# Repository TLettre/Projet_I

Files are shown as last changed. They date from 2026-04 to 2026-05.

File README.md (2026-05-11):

# Projet intégrateur 2: dashboard de trottinette
Projet Final de Projet Intégrateur 2.

## Mise en contexte

Le projet consiste à développer, programmer et assembler
un tableau de bord qui est fixé sur une trottinette électrique
complètement fonctionnelle à l’aide d’un boitier. Ce système 
électronique complet est supposé établir une communication avec le module
de contrôle, récupérer les données essentielles, traiter puis
présenter ces données ainsi que permettre au conducteur de visualiser
l’état du véhicule en temps réel.  

Dans ce fichier, il sera possible de voir la totalité des éléments présents autant en 
documentation que fonctionement au niveau du tableau de bord de la trottinette.

## Prérequis

### Matériel:
- Le PCB doit être alimenté avec 12V et 50mA.
- Le module de contrôle utilisé doit être le STM32U083CC.
- Le STM32U083CC doit être alimenté par un cable USB-C.
- Le dashboard doit être affiché sur un écran avec un cable USB-C à HDMI.
- Le PCB doit contenir un bouton de réinitialisation.
- Le branchement du connecteur JST qui est branché à la trottinette est définit dans le document de branchements.
- Nous avons ajouté des DELs d'alimentation pour chaque niveau d'alimentation, bien que ce requis était optionnel.
- Il doit y avoir 5mA maximum pour chaque DEL.
- Le PCB doit être fixé avec 4 vis M3.
- Nous avons fait la conception d’un boitier ergonomique pour encapsuler l’électronique, bien que ce requis soit optionnel.
- Le boitier doit pouvoir être bien fixé sur le guidon de la trottinette.
- Les dimmensions du PCB doivent être de 5cm par 5cm.
- Le PCB ne doit pas être accessible à l'usager.
- Les DELs d'alimentation ne doivent pas être accessibles à l'usager.
- Le boitier doit être simple à imprimer.

### Logiciel:
- Le module de contrôle et le tableau de bord doivent communiquer par protocole UART.
- Les données sont transmises par le module de contrôle dans un format JSON.
- Les informations suivantes doivent être affichées : la commande envoyée au moteur, la vitesse du véhicule, le pourcentage de charge de la batterie, le courant consommé, la température du système, l'état de l’éclairage, et l'information de freinage.
- L'affichage doit être ergonomique.
- L'information affichée doit être en temps réel.
- Le délai de rafraichissement doit être 4 fois par secondes.
- L'information affichée sur l'écran doit être épuré, clair, visible et compréhensible.

### Limitations:
- Nous ne connaissions pas l'ampleur du projet, ce qui a beaucoup affecté l'organisation de notre projet.

## Documentation

Voici les différents documents qui se retrouvent dans le Github ainsi que la fonction de chacun.

[**Boitier**:](https://github.com/TLettre/Projet_I/blob/a2e4f342a44780944c0242c8f5481d343143d4d6/Boitier.zip)
Le fichier Boitier.zip contient les documents de la modélisation du boitier 3D. Tous les fichiers qui étaient nécessaires à l'impression se trouvent dans ce fichier.

[**Cahier des charges**:](https://github.com/TLettre/Projet_I/blob/81377b3d7a6bdb845bd9907a101511ad725f1cf8/Cahier_charges.docx)
Ce fichier contient toutes les informations concernant le projet. 
- Mise en situation et schéma de concept (p.3)
- Requis techniques et inconnus u projet (p.4-5)
- Livrables et échéancier (p.5-6)
Ce fichier regroupe donc toutes les informations que nous avions concernant le projet.

[**Schéma bloc**:](https://github.com/TLettre/Projet_I/blob/feae1b3e02cbf4ebef9064a34becacfc2022ecb2/Notes/ProjetIntegrateur2.drawio)
Schéma qui explique le fonctionnement de notre PCB.

[**Schéma électrique**:](https://github.com/TLettre/Projet_I/blob/main/Altium/PI2_Circuit.SchDoc)
Ce fichier contien le schéma électrique du tableau de bord. 
- Le régulateur et la bobine ne sont pas les bonnes pièces.

[**PCB**:](https://github.com/TLettre/Projet_I/blob/main/Altium/PI2_PCB_2L.PcbDoc)
Fichier Altium du PCB complet du tableau de bord.
-  Les footprints de la bobine, du régulateur et des boutons ne sont pas les bonnes.

[**BOM**:](https://github.com/TLettre/Projet_I/blob/96cb56f76c8dbb2d10cd777ee212bbd68585368f/Altium/BOM.pdf)
Ce fichier contient les informations importantes de chacunes des pièces soudées sur le PCB.
-  La bobine et le régulateur ne sont pas les bonnes pièces et on été remplacées sur le PCB.

[**Code STM32**:](https://github.com/TLettre/Projet_I/blob/main/Code/code%20du%20stm32.c)
Code pour le fonctionnement du PCB.
- Il devrait prendre les données du fichier JSON et les envoyer vers le Raspberry Pi par UART.
- Des explications plus précises concernant le code se trouvent dans les commentaires du code.

[**Code Raspberry Pi**:](https://github.com/TLettre/Projet_I/blob/main/Code/code_pi.py)
Code qui permet de récupérer les donnés en JSON et de les envoyer sur l'écran.
- Des explications plus précises concernant le code se trouvent dans les commentaires du code.

Tout autre fichier de programmation sert à exécuter des tests.

## Guide d'utilisation

**Démarage**: Le tableau de bord devrait démarrer lorsque la trottinette est mise en marche.
		
### Mode de fonctionnement pour un utilisateur:
Les données ci-dessous devraient être visibles sur l'écran dès que la trottinette est activée:
- Vitesse de la trottinette (en km/h)
- Pourcentage de la batterie
- Courrant consommé (en ampères)
- Température du système (en degrés celsius)
- État de l'éclairage (on ou off)
- Information de freinage (on ou off)

Lorsque la trottinette est en mode freinage, il est impossible d'accélérer.
		
[**Image du Dashboard en action**](https://github.com/TLettre/Projet_I/blob/6009a4685d689ea0507f30d0aa41ed84b18c9245/Code/dashboard%20trotinette.png)

### Pour un développeur:
- La DEL D1 verte indique le fonctionnement du 12V.
- La DEL D2 rouge indique le fonctionnement 3.3V.
- Le bouton S1 permet de faire un RESET du PCB.
- Le bouton S2 permet de BOOTer le PCB pour envoyer un nouveau code dans le microcontrôleur.

## À terminer
- Le BOOT ne fonctionne pas, donc il faudrait l'arranger.
- La communication entre le PCB et le Raspberry Pi en UART ne fonctionne pas.

**Auteurs**: Amélie, Tristan et Gauthier

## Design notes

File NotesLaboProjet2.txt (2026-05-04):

Semaine 1
Tristan: 
	- recherche dans les fiches techniques et schéma électrique
	- recherche sur le régulateur switching et son branchement
	- branchement du régulateur switching
	- rechercher les pièces importantes et trouver leurs symboles dans Altium
	- faire les symboles et les traces des pièces s'ils n'existent pas
Amélie: 
	- recherche dans les fiches techniques et schéma électrique
	- recherche sur le régulateur switching et son branchement
	- branchement du régulateur switching
	- recherche sur le connecteur et son branchement
	- branchement du connecteur
Gauthier: 
	- recherche dans les fiches techniques et schéma électrique
	- recherche sur le régulateur switching et son branchement
	- branchement du régulateur switching
	- recherche sur le MCU et son branchement
	- commencer le branchement du MCU

- Nous avons créé les symboles et les traces des pièces dont nous ne les avions pas.
- Nous avons trouvé toutes les pièces importantes (écran, connecteurs, BMI323) dont nous avions besoin dans le schéma.
- Nous avons fait beaucoup de recherches sur le branchement du régulateur switching et nous avons fait le branchement.
- Nous avons débuté la recherche et le branchement du MCU
- Manque temps schéma électrique: sous estimé le temps et la recherche nécessaire, beaucoup temps recherche LDO

--------------------------------------------------------------------------------------------------------------------------------------------------------------------------------------------

Semaine 2
Tristan: 
	- continuer la recherche dans les fiches techniques et schéma électrique
	- finir recherche du MCU et son branchement
	- finir le branchement du MCU
	- recherche et branchement du BMI323
	- envoyer le BOM
Amélie: 
	- continuer la recherche dans les fiches techniques et schéma électrique
	- finir recherche du MCU et son branchement
	- finir le branchement du MCU
	- recherche et branchement du BMI323
	- envoyer le BOM
Gauthier: 
	- continuer la recherche dans les fiches techniques et schéma électrique
	- recherche et branchement de l'écran
	- recherche et branchement du BMI323
	- envoyer le BOM

- Nous avons fait la recherche et le branchement de l'écran
- Nous avons fait la recherche et le branchement du BMI323
- Nous avons terminé la recherche et le branchement du MCU
- Rencontre pour les reviews: nous avons décidé d'envoyer le BOM avant d'avoir eu la vérification du schéma
- Le client a changé certaines pièces à utiliser puisqu'il y avait une erreur. Il a donc fallu faire la recherche de ces pièces et les symboles si nécessaire.

--------------------------------------------------------------------------------------------------------------------------------------------------------------------------------------------

Semaine 3
Tristan: 
	- finir le schéma
	- brancher les DELs d'alimentation
	- finir le branchement de chaque pièce
	- brancher les pièces entre elles
	- séparer le schéma dans des parties clairement identifiées pour organiser le schéma
	- s'assurer d'avoir ajouté les notes nécessaires pour comprendre de le schéma
Amélie: 
	- finir le schéma
	- finir le branchement de chaque pièce
	- brancher les pièces entre elles
	- séparer le schéma dans des parties clairement identifiées pour organiser le schéma
	- s'assurer d'avoir ajouté les notes nécessaires pour comprendre de le schéma
Gauthier: 
	- finir le schéma
	- finir le branchement de chaque pièce
	- brancher les pièces entre elles
	- séparer le schéma dans des parties clairement identifiées pour organiser le schéma
	- s'assurer d'avoir ajouté les notes nécessaires pour comprendre de le schéma

- Nous avons fait la recherche et le branchement de chacun des connecteur
- Nous avons fait le branchement des DELs d'alimentation
- Nous avons organisé le schéma et identifié chaque partie du schéma

--------------------------------------------------------------------------------------------------------------------------------------------------------------------------------------------

Semaine 4
Tristan: 
	- corriger les erreurs du schéma
	- corriger certaines erreurs dans le schéma
	- faire le routage du PCB
	- finir le routage du PCB en dehors du cours
	- régler les problèmes du schéma et du PCB
Amélie: 
	- corriger les erreurs du schéma
	- faire le boitier
	- finir la modélisation du boitier en dehors du cours
	- aider Tristan à finir le schéma
	- il faut attendre que le schéma soit fini afin de commencer la modélisation pour avoir les mesures du PCB, ce qui a retardé la modélisation du boitier
	- régler les problèmes du schéma et du PCB
Gauthier: 
	- commencer le code
	- faire la recherche nécessaire (sur le Raspberry Pi) afin de pouvoir faire le code
	- préparer le corps du code (les parties nécessaires et comment le code sera construit)
	- faire la recherche nécessaire pour commencer à coder les parties essentielles
	- régler les problèmes du schéma et du PCB

- Nous avons du annuler plusieurs reviews puisque le schéma nous a demandé beaucoup plus de temps que ce que nous avions prévu.
- L'écran a été remplacé par un Raspberry Pi. Nous avons dû faire la recherche pour le Raspberry Pi puisque ce remplacement était un imprévu.
- Lors de cette semaine, nous avons du faire beaucoup de travail en dehors du cours pour finir les livrables à temps.
- Nous avons commencé à faire beaucoup plus de documentation concernant notre travail et l'utilisation de notre projet.

--------------------------------------------------------------------------------------------------------------------------------------------------------------------------------------------

Semaine 5
Tristan: 
	- créer un GitHub pour y mettre tous ce qui a été fait pour le projet jusqu'à maintenant
	- commencer le guide d'utilisateur
		=> explication des modes dans le guide d'utilisateur
		=> explication du démarrage
		=> explication de ce qui est afficher
Amélie:
	- terminer le boitier
	- vérifier que les mesures du boitier fonctionnent avec le PCB
	- faire imprimer le boitier
	- commencer le plan de tests
		=> prendre le gabarit utilisé dans le cours de Circuit Imprimé 2
		=> remplir l'entête du document
		=> commencer à inscrire les tests qui devront être fait
Gauthier:
	- faire les recherches nécessaires pour la programmation
	- commencer la programmation
		=> créer des espaces/fenêtres pour chaque chose qui devra être affichée

- Nous avons décidé de commencer le guide d'utilisateur plus tôt afin de recevoir le plus de commentaires possibles lors de la rétroaction formative.
- L'écran ne doit plus être utilisé dans le projet, donc nous avons moins de recherches à faire cette semaine ce qui nous permet de prendre de l'avance.
- Nous avons créé un GitHub pour y mettre tous ce que nous avons fait dans le projet jusqu'à maintenant.

--------------------------------------------------------------------------------------------------------------------------------------------------------------------------------------------

Semaine 6
Tristan:
	- terminer de mettre tous les fichiers dans le Github
	- continuer le guide d'utilisateur
	- continuer le plan de tests
	- aider Gauthier avec le code
Amélie:
	- correction des mesures du boitier
	- réimprimer le boitier corrigé
	- finir le plan de test
Gauthier:
	- continuer la programmation
		=> finir la fenêtre d'interface
		=> afficher les informations reçues par le microcontrôleur
		=> recherche et amélioration du code de l'interface graphique 
		=> revoir certains bloc comme la vitesse
		=> améliorer le mode erreur

- Nous avons fait une analyse de rétroaction formative avec l'enseignant.
- Nous n'avons pas reçu le PCB que nous avons fait. Nous avions prévu de le recevoir cette semaine et de faire la soudure. Cette partie de la planification doit donc être reportée.

--------------------------------------------------------------------------------------------------------------------------------------------------------------------------------------------

Semaine 7
Tristan:
	- Tristan était absent et n'a pas eu l'occasion d'avancer le projet pendant la semaine
Amélie:
	- finir le plan de test
	- continuer le guide d'utilisateur
Gauthier:
	- continuer la programmation
		=> début du code pour la transmission en UART
		=> traduction du JSON dans le code STM32 puis renvoie les données brutes dans le rasberry

- Tristan était absent pendant cette période. Il n'a donc pas pu faire la soudure pendant le cours. Il va falloir travailler d'avantage pendant la semaine pour rattraper notre retard et redistribuer les tâches pour ce cours si nécessaire.
- Tristan est absent et n'a pas mis le guide d'utilisateur (commencé et presque terminé) sur le GitHub. Il est le seul à y avoir accès. Il va devoir le mettre dans le Github dès que possible et l'envoyer à l'enseignant rapidement pour avoir la rétroaction formative du guide d'utilisateur.
	=> Tristan a envoyé le guide d'utilisateur. Le guide d'utilisateur a été ajouté au GitHub et envoyé à l'enseignant pour la rétroaction formative.

--------------------------------------------------------------------------------------------------------------------------------------------------------------------------------------------

Semaine 8
Tristan: 
	- déterminer les pièces qui devront être soudées sur le PCB
	- prendre les pièces disponibles en classe
	- demander les pièces au magasin
	- faire la soudure lorsque les pièces seront reçues
	- faire la documentation de la partie électronique du projet dans le guide d'utilisateur
Amélie:
	- continuer le guide d'utilisateur
	- déterminer les tests nécessaires pour le boitier dans le plan de tests
	- faire la documentation de la partie mécanique du projet dans le guide d'utilisateur
Gauthier: 
	- terminer la programmation
		=> abandonner l'idée de traduire le code STM et juste créer un canal ouvert pour le STM il transfert juste les données sans décodera
		=> avancement sur le code du stm32
	- déterminer les tests nécessaires pour la programmation dans le plan de tests
	- faire la documentation de la partie programmation du projet dans le guide d'utilisateur
	
- Puisque nous n'avions pas les pièces pour souder le PCB, nous n'avons pas eu l'occasion de faire la soudure lors de la semaine précédente. Tristan devra donc faire la soudure pendant la semaine lorsque les pièces seront reçues.
- Nous avons eu de la difficulté à obtenir une version à jour du BOM. Nous avons fait quelques changements au schéma électrique entre la remise du BOM et la remise du PCB. Nous n'avons ajouté que quelques petites pièces faciles à avoir (résistances). 
- Lorsque nous avons reçu nos pièce, il y avait une inductance que le magasin n'avait pas. Il n'y avait aucun équivalent de cette pièce. Nous avons donc du chercher une autre inductance qui pourrait fonctionner dans notre circuit.
- Les traces prévues pour l'inductance sont en surface mount, alors que l'inductance est pour du through hole, ce qui rend la soudure plus difficile. Heureusement, la place dédiée à l'inductance était proche du bord du PCB. Nous l'avons donc soudue de côté.
- L'inductance de remplacement est beaucoup plus grosse que la précédente. Nous avons donc dû faire un trou dans notre boitier pour que le PCB soudé puisse entrer dans le boitier.
- Les boutons étaient trop petits pour les traces dédiées. Nous avons donc dû faire des ponds de soudure entre les boutons et les pads.

--------------------------------------------------------------------------------------------------------------------------------------------------------------------------------------------

Semaine 9
Tristan:
	- terminer la soudure du PCB
	- remplir le plan de test du PCB
	- faire l'intégration
	- aider Gauthier avec les tests pour le code
Amélie:
	- terminer le guide d'utilisateur
	- préparer la présentation
	- faire et compléter le plan de tests pour le boitier
	- faire l'intégration
Gauthier:
	- tester la programmation avec le Raspberry Pi
	- faire la documentation de la partie programmation du projet dans le guide d'utilisateur
	- remplir le plan de test de la programmation
	- faire l'intégration

- La remise formative du guide d'utilisateur n'a pas été faite. Il y a eu une mauvaise communication dans l'équipe. Nous avons donc remis le guide d'utilisateur en retard et nous avons eu les commentaires de l'enseignant en retard.
- Nous n'avions pas regardé les commentaires de l'enseignant sur les choix des pièces dans le BOM. Le régulateur que nous devions mettre ne fonctionne donc pas. Nous avons donc du souder des fils et alimenter la sortie du régulateur avec du 3.3V pour être en mesure d'exécuter les tests.
- Le prototype n'est toujours pas fonctionnel. Le PCB supporte les tensions et les del de statut fonctionnent. L'ordinateur semble capter le Raspberry Pi et le code semble être envoyé. Donc, la programmation ne fonctionne probablement pas. Sinon, il pourrait y avoir un problème pour la connection entre le PCB et le Raspberry Pi.
- Il y a eu des problèmes avec la programmation. Le code a été testé avant qu'il soit terminé. Certaines fonctions étaient définies, mais pas appelées. Les librairies qui étaient nécessaires au code n'étaient pas envoyées dans le GitHub. Le code manque énormément de commentaire, ce qui rend le code difficile à comprendre pour les autres coéquipiers. Il y a certains aspects du code qui n'ont pas été appris en classe, ce qui rend le code peu commenté encore plus difficile à comprendre pour les autres coéquipiers.
- Le boitier n'était pas assez grand pour un des condensateur. Il a donc fallu faire un autre trou dans le couvercle du boitier pour que le boitier puisse se fermer.

--------------------------------------------------------------------------------------------------------------------------------------------------------------------------------------------

Semaine 10
Tristan:
	- faire fonctionner le prototype du projet
	- terminer de remplir le plan de tests
	- terminer le guide d'utilisateur
	- présenter notre projet
Amélie:
	- faire fonctionner le prototype du projet
	- terminer de remplir le plan de tests
	- terminer le guide d'utilisateur
	- présenter notre projet
Gauthier:
	- faire fonctionner le prototype du projet
	- terminer de remplir le plan de tests
	- terminer le guide d'utilisateur
	- présenter notre projet

- Nous avons réalisé que le BOOT de notre PCB ne fonctionne pas. Afin de régler ce problème, il faudrait refaire le PCB, puisque nous pensons que le problème est dans notre branchement. Nous n'avons pas le temps de régler ce problème, donc notre prototype ne fonctionne pas.
- Nous sommes incapable d'envoyer notre code dans notre PCB. Nous pensons que c'est en raison du  mauvais fonctionnement de notre circuit de BOOT.

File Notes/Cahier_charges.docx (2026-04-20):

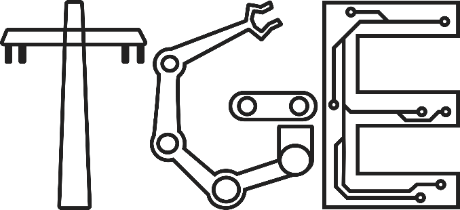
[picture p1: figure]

Technologie du génie électrique : Électronique programmable (243.G0)

TITRE
Amélie Sarrazin
Tristan Lettre
Gauthier Milossi

243-494-SH - Projet intégrateur 2
Présenté à : Prénom Nom

Date :

Table des matières

# 1. Mise en situation

## A. Acteurs du projet

- Équipe professorale de TGÉ du Cégep de Sherbrooke
- M. Gauthier (représentant d’ÉcoMobilité Sherbrooke)
- Les étudiants (public cible)
- Notre équipe

## B. Résumer du mandat

Le mandat consiste à développer, programmer et assembler un tableau de bord qui sera fixée sur une trottinette électrique complètement fonctionnelle, à l’aide d’un boitier. Ce système électronique complet devra établir une communication avec le module de contrôle, récupérer les données essentielles, traiter puis présenter ces données ainsi que permettre au conducteur visualiser l’état du véhicule en temps réel.

## C. Schéma de concept

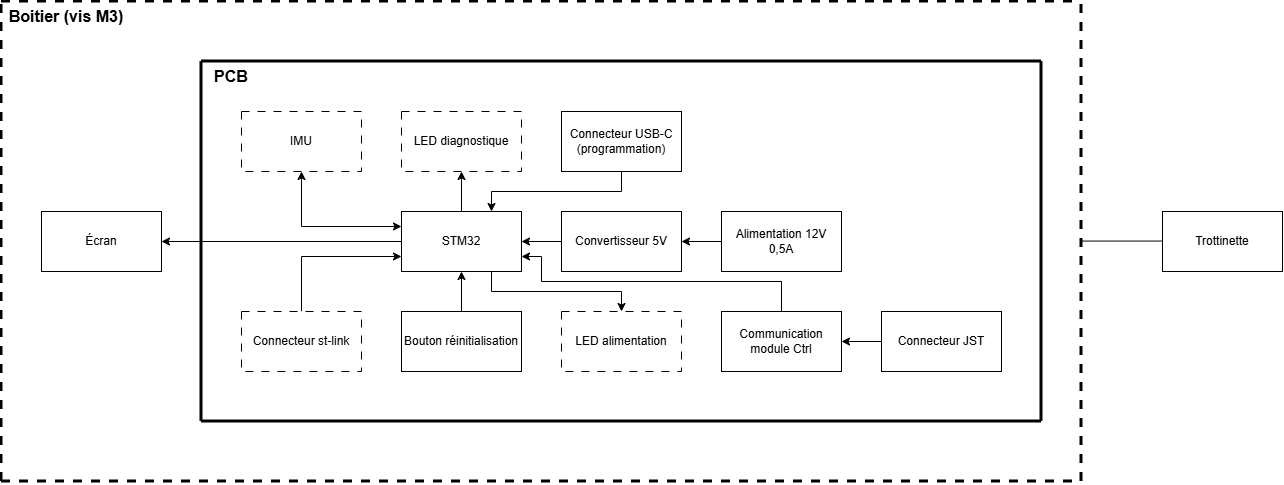
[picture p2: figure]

# 2. Requis technique

## A. Électrique

I. Essentiel | II. Optionnel
- Alimentation 12V 5mA - Module de contrôle (STM32U083MC) - STM32 (connecteur USB-C) - Écran (SMRVT50HQSFWN00) - Bouton de réinitialisation - Connecteur JST (branchement dans schéma) - Protocole UART entre le module de contrôle et le tableau de bord | - DEL d’alimentation pour chaque niveau d’alimentation - 2 DELs pull-up sur les broches GPIO 18 et 21 - 2 DELs pull-down sur d’autres broches GPIO - 5mA maximum pour chaque DEL - Connecteur ST-link - Accéléromètre (BMI323) - 2 boutons débogage

## D. Informatique

III. Essentiel | IV. Optionnel
- Protocole UART entre le module de contrôle et le tableau de bord - Données transmises par le module de contrôle dans un format JSON (spécifications envoyées par mio) - Informations affichées : Commande envoyée au moteur, vitesse du véhicule, pourcentage de charge de la batterie, courant consommé, température du système, état de l’éclairage, information de freinage (grisement de commande à l’écran) - Affichage ergonomique - Informations en temps réel - Délai de rafraichissement : 4 fois par secondes - Information sur l’écran : épuré, clair, visible et compréhesible | - 3 modes : initialisation, conduite et erreur - Mode conduite : affichages donnés facilement lisibles - Modes initialisation/erreur : affichage informations diagnostique spécifiques (codes erreur, état bouton arrêt urgence et état activation système) - Développement de code pour l’IMU - Logiciel de débogage

## E. Mécanique

V. Essentiel | VI. Optionnel
- Fixer le PCB avec 4 vis M3 - Fixé sur le guidon de la trottinette - Si l’IMU est présent, IMU centré et horizontal sur la carte - Essayer de garder le PCB 5 cm x 5 cm - PCB pas accessible à l’usager - Diodes d’alimentations pas visibles pour l’utilisateur - Écran bien visible à l’utilisateur - Boitier simple à imprimer - Boitier bien fixé au guidon | - Conception d’un boitier ergonomique pour encapsuler l’électronique

## F. Inconnus/risques

- Pinout du JST à 8 broches (branchement déjà défini, mais inconnu)
- Vitesse de transfert des données/affichage (temps réel)
- Est-ce qu’il faut que le projet soit résistant à l’eau?
- Requis de la résistance au climat
- Matériel du boitier
- Comment connecter fils au contrôleur?
- Communication entre carte et écran
- Taille de la trottinette/volant
- Structure/format du JSON
- Spécifications ergonomiques
- Ampleur du projet

## G. Livrables

- Prototype fonctionnel (circuit imprimé, assemblé, programmé et idéalement dans un boitier)
- Plan de test du prototype
- Guide utilisateur (explique comment utiliser interface)
- Documentation de fabrication complète (schéma électrique, dimensions, matériaux, fichier altium/fabrication et code)
- Présentation et démonstration

# 3. Échéancier

Bloc de travail (4h/semaine) | Tâches | | | Livrable
| Équipier 1 : Amélie | Équipier 2 : Tristan | Équipier 3 : Gauthier
1 | Lecture datasheets + schéma électrique | Lecture datasheets + schéma électrique | Lecture datasheets + schéma électrique | Dépôt cahier des charges
2 | Review schéma + BOM | Review schéma + BOM | Review schéma + BOM | Remise BOM
3 | Modélisation 3D | Routage | Configuration IOE et Github + programmation trottinette → PCB → écran
4 | Review modélisation 3D + routage + prog + fab PCB | Review modélisation 3D + routage + prog + fab PCB | Review modélisation 3D + routage + prog + fab PCB | Fab PCB + impression 3D
5 | Imprimer boitier + recherches/choisir protocole écran | Recherche + programmation StLink | Programmation trottinette → PCB → écran + mockup graphic + programmer graphic
6 | Assemblage boitier + plan de tests boitier | Soudage PCB + plan de tests PCB | Finir programmation | Analyse rétro formatif
7 | Intégration + plan de tests | Intégration + plan de tests | Intégration + plan de tests | Évaluation formative guide utilisateur
8 | Guide utilisateur + préparation présentation | Guide utilisateur + préparation présentation | Guide utilisateur + préparation présentation | Prototype fonctionnel
9 | Période buffer | Période buffer | Période buffer | Guide utilisateur
10 | | | | Présentation
11 | | | | Analyse rétro + guide utilisateur

Titre du projet

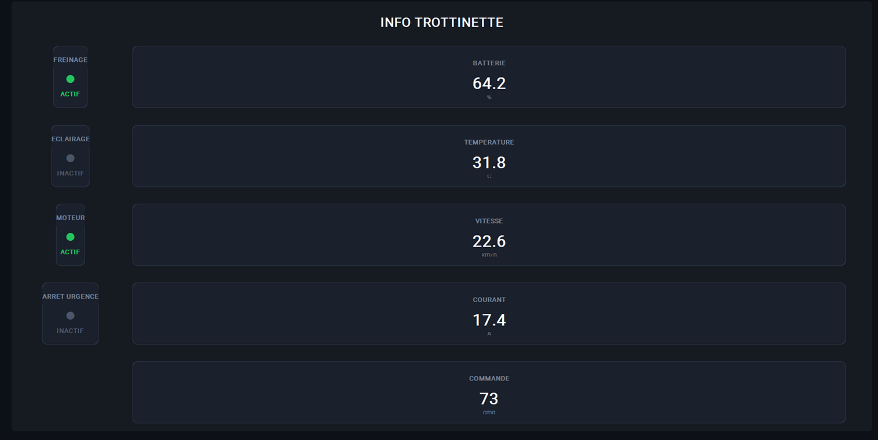
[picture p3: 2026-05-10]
Code/dashboard trotinette.png

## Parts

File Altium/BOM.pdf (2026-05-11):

Board | 1
Cours | 00

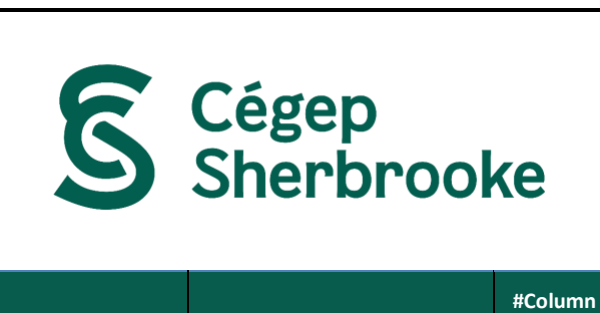
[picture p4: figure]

Item # | Designator | Layer | Description | Comment | Package / Case | Supplier 1 | Supplier Part Number 1 | Quantity | Quantity Total | #Column Name Error:' Note
1 | C1 | Top | WCAP-ASLI Aluminum Electrolytic Capacitors | 865080442004 | | | | 1 | #REF!
2 | C2 | Top | CAP ALUM 220UF 20% 25V SMD | EEE-1EA221UP | | | | 1 | #REF!
3 | C3 | Top | CAP CER 1UF 10V | 1µF | 0805 (2012 Metric) | DigiKey | 478-10611-1-ND | 1 | #REF!
4 | C4, C5 | Top | CAP CER 0.1UF | 0.1 µF | 0603 (1608 Metric) | DigiKey | 399- | 2 | #REF!
5 | D1 | Top | WURTH | 150080GS75000 | | | | 1 | #REF!
6 | D2 | Top | LED Uni-Color Red | 150080RS75000 | | | | 1 | #REF!
7 | J1 | Top | CONN HEADER | S10B-PHDSS (LF)(SN) | | | | 1 | #REF!
8 | J2 | Top | CONN RCP USB2.0 | DX07S016JA1R1500 | | | | 1 | #REF!
9 | J3 | Top | Connector Header | TSW-102-23-T-S | | | | 1 | #REF!
10 | L1 | Top | INDUCTOR, | B82432C1334K000 | | | | 1 | #REF!
11 | R1 | Top | RES 2K OHM 1% | 2 kOhms | 0603 (1608 Metric) | DigiKey | RMCF0603FT2K00CT-ND | 1 | #REF!
12 | R2 | Top | RES 270 OHM 1% | 270 Ohms | 0603 (1608 Metric) | DigiKey | 2019-RK73H1JTTD2700FCT-1 | | #REF!
13 | R3, R4 | Top | RES SMD 5.1K | 5.1 kOhms | 0603 (1608 Metric) | DigiKey | YAG3621CT-ND | 2 | #REF!
14 | R5 | Top | RES SMD 100K | | | | | 1 | #REF!
15 | S1, S2 | Top | SWITCH TACTILE | FSM4JSMA | | DigiKey | 450-1129-ND | 2 | #REF!
16 | U1 | Top | LM2574N-ADJG | LM2574N-ADJG | | | | 1 | #REF!
17 | U2 | Top | MCU 32-bit ARM | STM32U083CCT6 | | | | 1 | #REF!
18 | U3 | Top | Description | BMI323 | | | | 1 | #REF!

# Bill of Material

PI_2 | Concepteur Principal amélie
PI2 (243-494-SH) | Date du projet 09/02/26
Département Technologies du génie électrique | Date de génération du BOM 2026-04-20
Révision #NAME? | Heure de génération du BOM 10:01
Nombre de PCB 1 | Variant None

Commentaires ou instruction spécialies

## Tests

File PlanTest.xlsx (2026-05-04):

 |  | Plan de tests
 | Nom du PCB | PI_2 | Préparé par | Amélie Sarrazin
 | Cours | Projet Intégrateur 2 | Testeur | Tristan Lettre et Amélie Sarrazin
 | Département | Technologies du génie électrique | date | 2026-03-30
 | Révision du PCB
 | Fonction | Description du test | Résultat | Raison réussite ou échec | modification effectuée | Nouveau résultat | Commentaire
Électrique | Unitaire | Faire une inspection visuelle du PCB. | Réussi | Le PCB n'est pas endommagé, sauf pour des vias qui ne sont pas couverts et des pads un peu abimés. Les soudures sont correctes. Il n'y a aucun court-circuit. Il semble encore y avoir du flux qui pourrait causer des court-circuits, mais des tests de continuité ont été exécutés pour vérifier qu'il n'y a aucun court-circuit.
 | Unitaire | Vérifier qu'il n'y a aucun court-circuit entre le 12V et le GND, en mesurant la résistance. | Réussi | La résistance entre le 12V et le GND est de 42MΩ.
 | Unitaire | Vérifier qu'il n'y a aucun court-circuit entre le 3.3V et le GND, en mesurant la résistance. | Réussi | La résistance entre le 3.3V et le GND est de 4.4MΩ.
 | Fonctionnel | Brancher le PCB afin de vérifier s'il peut être alimenté ou non (smoke test). Les DELs d'alimentation devraient être allumées. | Réussi | Les LEDs de statut du 12V et du 3.3V allument toutes les deux. Le PCB n'émet pas de chaleur et il n'y a aucun comportement du PCB qui indiquerait qu'il ne fonctionne pas.
 | Fonctionnel | Brancher le PCB à la trottinette et vérifier qu'il y a bien 12V à l'entrée du régulateur de tension. | Réussi | Nous n'avons pas de régulateur de tension, ce qui pourrait légèrement affecter ce test. Lorsque le PCB est alimenté, il y a 11.998V à la broche dédiée à l'entrée du régulateur de tension.
 | Fonctionnel | Vérifier qu'il y a bien 3.3V à la sortie du régulateur de tension. | Réussi | Nous n'avons pas de régulateur de tension, donc nous devons alimenter le PCB avec une source de tension externe. À la broche dédiée à la sortie du régulateur, il y a 3.299V.
 | Fonctionnel | Mesurer la tension lorsque le bouton SW1 n'est pas appuyé. Puis, appuyer sur le bouton et mesurer la tension. La tension mesurée devrait passer de 3.3V à 0V. | Réussi | Lorsque ce test est exécuté, l'oscilloscope montre que la tension passe d'environ 3.3V à 0V.
 | Fonctionnel | Mesurer la tension lorsque le bouton SW2 n'est pas appuyé. Puis, appuyer sur le bouton et mesurer la tension. La tension mesurée devrait passer de 0V à 3.3V. | Réussi | Lorsque ce test est exécuté, l'oscilloscope montre que la tension passe de 0V à environ 3.3V.
Programmation | Intégration | Mettre le code dans le Raspberry Pi et le bancher au PCB et à l'écran. L'affichage devrait être visible sur l'écran. | Réussi | La fenêtre d'affichage est visible sur l'écran. Il y a des informations qui sont inscrites là où les devrait être inscrites.
 | Intégration | Transmettre des données au PCB et au Raspberry Pi avec du UART. | Échec | Le PCB et le Raspberry Pi ne peuvent pas communiquer ensemble puisque nous sommes pas capable d'envoyer le code dans notre PCB et le Raspberry Pi est incapable de recevoir des informations par UART, puisque nous sommes incapable d'accéder au port. Nous ne pouvons donc pas faire ce test. De plus, dans notre PCB, les broches de UART du STM32 vers le Raspberry Pi sont inversées. Il faut donc les brancher de façon inverse lorsque nous faisons des tests. | Nous pensons que le problème de notre PCB est le fonctionnement du BOOT. Donc, afin de réussir ce test, nous devrier refaire entièrement la partie du BOOT. | Échec | Cette modification nécéssiterait probablement de refaire le PCB. Nous n'avons pas le temps de régler le problème.
 | Intégration | Vérifier que les mesures affichées sur l'écran concordent avec les mesures reçues dans le fichier JSON. | Réussi | Les données affichées sont les mêmes qui se retrouvent dans le fichier JSON que nous avons créé pour tester cette partie du code. Lorsqu'une des données est modifiée, l'affichage affiche la nouvele donnée.
 | Intégration | Envoyer les informations du PCB au Raspberry Pi et les afficher sur l'écran. | Échec | Le PCB et le Raspberry Pi ne peuvent pas communiquer ensemble puisque nous sommes pas capable d'envoyer le code dans notre PCB et le Raspberry Pi est incapable de recevoir des informations par UART, puisque nous sommes incapable d'accéder au port. Nous ne pouvons donc pas faire ce test. De plus, dans notre PCB, les broches de UART du STM32 vers le Raspberry Pi sont inversées. Il faut donc les brancher de façon inverse lorsque nous faisons des tests. | Nous pensons que le problème de notre PCB est le fonctionnement du BOOT. Donc, afin de réussir ce test, nous devrier refaire entièrement la partie du BOOT. | Échec | Cette modification nécéssiterait probablement de refaire le PCB. Nous n'avons pas le temps de régler le problème.
Mécanique | Fonctionnel | Vérifier que le boitier se ferme. | Réussi | Le boitier se ferme.
 | Fonctionnel | Vérifier que les trous dédiés aux vis sont de la bonne grandeur. | Réussi | Les vis entrent dans les trous et tiennent bien.
 | Fonctionnel | Tourner le boitier à l'envers. Le couvercle du boitier ne devrait pas tomber. | Échec | Lorsque le boitier est tourné sur le côté ou à l'envers, le couvercle ne tient pas. | J'ai modifié les mesure du couvercle et je l'ai réimprimer pour que le couvercle tienne lorsque le boitier est tourné. | Réussi | Le boitier reste fermé lorsqu'il est tourné à l'envers.
 | Fonctionnel | Mettre le PCB soudé dans le boitier et vérifier qu'il se ferme correctement. | Échec | Il y avait une inductance qui était trop grande. Elle empèchait le PCB d'entrer dans le boitier. Il y avait également un condensateur qui empêchait le boitier de fermer. | Des trous ont été ajoutés dans le boitier pour l'inductance et le condensateur. | Réussi | Le boitier se ferme.
 | Fonctionnel | Vérifier que les connecteurs peuvent entrer dans leur trous désignés. | Réussi | Chaque connecteur entre dans les trous et peut être branché sur le PCB lorsqu'il est à l'intérieur du boitier.

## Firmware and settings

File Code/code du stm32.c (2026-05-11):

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
/* Includes ------------------------------------------------------------------*/
#include "main.h"
#include "usart.h"
#include "usb.h"
#include "gpio.h"
#include <string.h>

// Variables globales
uint8_t rx_byte [512]; // buffer pour le data qui est reçu ou envoyé



/* USER CODE END PV */

void SystemClock_Config(void);
/* USER CODE BEGIN PFP */



void HAL_UART_RxCpltCallback(UART_HandleTypeDef *huart)
{
   
    
        /* Transmettre immédiatement l'octet reçu sur LPUART2 */
        HAL_UART_Transmit(&hlpuart2, &rx_byte, 1, 10);
        
        /* Redémarrer la réception */
        HAL_UART_Receive_IT(&hlpuart1, &rx_byte, 1);
    
}
/* USER CODE END PFP */

/**
  * @brief  The application entry point.
  * @retval int
  */
int main(void)
{

  /* MCU Configuration--------------------------------------------------------*/

  /* Reset of all peripherals, Initializes the Flash interface and the Systick. */
  HAL_Init();

  /* Configure the system clock */
  SystemClock_Config();

  /* Initialize all configured peripherals */
  MX_GPIO_Init();
  MX_LPUART1_UART_Init();
  MX_LPUART2_UART_Init();
  MX_SPI1_Init();
  MX_USB_PCD_Init();
//activer la reception uart
  HAL_UART_Receive_IT(&hlpuart1, &rx_byte, 1);
  /* Infinite loop */
  /* USER CODE BEGIN WHILE */
  while (1){


    /* USER CODE BEGIN 3 */
  }
  /* USER CODE END 3 */


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


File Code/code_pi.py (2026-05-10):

#installer la librarie custom tkinter
#installer python 3 avant dans l'invite de commande du rasberry pi
#procedure installer lib pour rasberry

#python3 -m venv venv
#source venv/bin/activate
#pip install customtkinter
#pip install pyserial
# les 2 autres librairie sont déja disponible

import customtkinter as ctk
import json
import serial
# a voir pour la connexion avec la carte
port = serial.Serial("COM3", baudrate=115200, timeout=1)
def lecture_uart(port): #changer dans mettre a j affichage à la place de lire données test / fonction qui permet de lire des infos sur un port UART

    donees1 = port.readline()
    données2 = donees1.decode("utf-8").strip()
    donnees_utile = json.loads(données2)

    return donnees_utile

def lire_donnees_test():# fonction test qui permet de lire un fichier json
    with open("cme.cpp", "r", encoding="utf-8") as fichier:
        return json.load(fichier)


def utilisation_donnees(donnees_utile): # cette fonction permet de stockées toutes les infos du fichiers json dans des variables que l'ont va utiliser dans la suite du code
    ctrl = donnees_utile["ctrl"]
    drive = donnees_utile["drive"]

    frein = ctrl["break_active"]
    estop = ctrl["estop_active"]
    moteur_on = ctrl["enable_active"]
    eclairage = ctrl["light_active"]
    commande = ctrl["cmd"]

    temperature = drive["temperature"]
    batterie = drive["battery_percentage"]
    courant = drive["motor_current"]
    vitesse = drive["speed"]

    return {
        "frein": frein,
        "estop": estop,
        "moteur_on": moteur_on,
        "eclairage": eclairage,
        "commande": commande,
        "temperature": temperature,
        "batterie": batterie,
        "courant": courant,
        "vitesse": vitesse,
    }


class App(ctk.CTk): # cette class nous permet de definir les paramètres principaux de l'app
    def __init__(self):
        super().__init__()
        self.geometry("1000x1000") # on defini la taille de l'écran ainsi que son titre de l'écran et sa place dans l'affichage
        self.title("dashboard_trotinette")
        self.configure(fg_color="#0d1117")

        self.grid_rowconfigure(0, weight=1)
        self.grid_columnconfigure(0, weight=1)

        self.frame_drive = InfoConduite(self, fg_color="#161b22")# cela nous permet de définir la police d'écriture
        self.frame_drive.grid(row=0, column=0, padx=25, pady=25, sticky="nsew")
        self.mettre_a_jour_test()

    def mettre_a_jour_test(self): # permet de mettre à jour l'affichage des données dans le code toute les secondes
        self.frame_drive.mettre_a_jour_affichage(lire_donnees_test())
        self.after(1000, self.mettre_a_jour_test)


class InfoConduite(ctk.CTkFrame): # cela permet de créer les case dans lesquelles les informations vont etre placées
    def __init__(self, master, **kwargs):
        super().__init__(master, **kwargs)

        self.grid_rowconfigure(0, weight=0)
        for row in range(1, 6):                     # on creer les espaces pour ageancer les infos dasn l'affichage
            self.grid_rowconfigure(row, weight=1)
        self.grid_columnconfigure(0, weight=0, minsize=230)
        self.grid_columnconfigure(1, weight=1)

        self.titre = ctk.CTkLabel( # creer le titre de l'application tout en haut de l'écran ( taille / police/ couleur)
            self,
            text="INFO TROTTINETTE",
            font=ctk.CTkFont(size=22, weight="bold"),
            text_color="white",
        )
        self.titre.grid(row=0, column=0, columnspan=2, pady=(22, 12), sticky="n")

        self.case_batterie = CaseInfo(self, "Batterie", "%") # cela creer tout les cases infos en fonctions des variables grace à la class Case info
        self.case_temperature = CaseInfo(self, "Temperature", "C")
        self.case_vitesse = CaseInfo(self, "Vitesse", "km/h")
        self.case_courant = CaseInfo(self, "Courant", "A")
        self.case_commande = CaseInfo(self, "Commande", "cmd")

        self.case_batterie.grid(row=1, column=1, padx=(25, 45), pady=14, sticky="nsew") # cela place les cases dasn l'affichage quelle collonne et que ligne 
        self.case_temperature.grid(row=2, column=1, padx=(25, 45), pady=14, sticky="nsew")
        self.case_vitesse.grid(row=3, column=1, padx=(25, 45), pady=14, sticky="nsew")
        self.case_courant.grid(row=4, column=1, padx=(25, 45), pady=14, sticky="nsew")
        self.case_commande.grid(row=5, column=1, padx=(25, 45), pady=14, sticky="nsew")

        self.case_frein = CaseOnOff(self, "Freinage") # on creer une autre case mais celle si creer un voyant qui s'llume dans la variable est ON
        self.case_eclairage = CaseOnOff(self, "Eclairage")
        self.case_moteur = CaseOnOff(self, "Moteur")
        self.case_estop = CaseOnOff(self, "Arret urgence")

        self.case_frein.grid(row=1, column=0, padx=(35, 15), pady=14, sticky="n") # on les places aussi dans l'affichage
        self.case_eclairage.grid(row=2, column=0, padx=(35, 15), pady=14, sticky="n")
        self.case_moteur.grid(row=3, column=0, padx=(35, 15), pady=14, sticky="n")
        self.case_estop.grid(row=4, column=0, padx=(35, 15), pady=14, sticky="n")

    def mettre_a_jour_affichage(self, donnees_utile): # cela sert a mettre à jour les infos recus dans le fichier json ou bien recus dans l'UART
        donnees = utilisation_donnees(donnees_utile)

        self.case_frein.mettre_a_jour(donnees["frein"])
        self.case_eclairage.mettre_a_jour(donnees["eclairage"])
        self.case_moteur.mettre_a_jour(donnees["moteur_on"])
        self.case_estop.mettre_a_jour(donnees["estop"])

        self.case_vitesse.mettre_a_jour(donnees["vitesse"])
        self.case_temperature.mettre_a_jour(donnees["temperature"])
        self.case_batterie.mettre_a_jour(donnees["batterie"])
        self.case_courant.mettre_a_jour(donnees["courant"])
        self.case_commande.mettre_a_jour(donnees["commande"])
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

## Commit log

2026-04-20 Create code de l'écran
    code du design de l'écran v1 potentiellement améliorable
2026-04-27 Create code du stm32
2026-04-27 prise de notes des semaines gauthier
2026-04-27 Rename code de l'écran to code de l'écran.py
2026-04-27 Rename code de l'écran.py to code_pi.py
2026-04-29 Update code du stm32
2026-04-29 Rename code du stm32 to code du stm32.c
2026-05-03 Update code du stm32.c
2026-05-04 Rename code du stm32.c to Code/code du stm32.c
2026-05-04 Rename PDT_PI_2 1.xlsx to PlanTests.xlsx
    [PlanTests.xlsx]
2026-05-10 ajout de commentaire

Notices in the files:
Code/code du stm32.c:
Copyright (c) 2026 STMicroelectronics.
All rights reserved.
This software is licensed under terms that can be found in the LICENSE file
